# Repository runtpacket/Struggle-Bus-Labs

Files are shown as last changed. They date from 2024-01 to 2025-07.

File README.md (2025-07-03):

## Struggle Bus Labs V2.3824
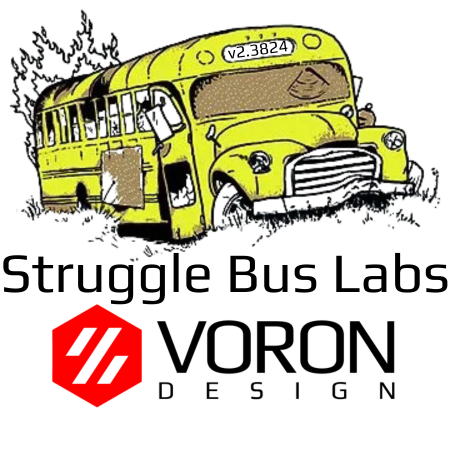
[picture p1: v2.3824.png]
Struggle Bus Labs


Come along and ride on a fantastic voyage with my Voron 2.4 350mm 3D Printer, I have named the Struggle Bus!

I hope you dont expect this to be cohert or organized.  this page is mainly for me to remeber thingds about my voron. 

## Build Log
Starting to prep for a toolhead change. Either XOl or Dragon Burner. Eitehr one will need filament cutter and runout sensor. Had an issues with end of sppol not coming of and jaming. this leaves the dub switch based fila runout in a good state. need to work on that. but next up  is https://github.com/bythorsthunder/Voron_Mods/tree/main/Wristwatch_Extruder_BMG

tonight I was playing with Multi Color printing. I tried all slicers each had littel quirks with thier setup for doing this. While researching I stumbled up 
[Single Extruder Tool Changer MMU with single exrtuder](https://github.com/strayr/klipper-fake-toolchanger/blob/main/README.md)

Setup is straight forward. Upload the klipper-fake-toolchanger.crg and add the include. then set up how many exturders in your slicer. no need to put M600 in for tool changer code as it will take care of that in th macro. Pretty slick. 

## My Build
Hoping to add the following to my machine this week
https://github.com/Thomas-3D/Front_Decontaminator
and an ERCF V2 with Happyhare in the future
https://github.com/moggieuk/Happy-Hare

[Formbot Voron 2.4R1 350mm Kit.](https://www.formbot3d.com/products/voron-24-pro-corexy-3d-printer-kit-with-hdmi-5-touch-screen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)

Dragon Std hot End, I print a lot of PLA. 5/11/2024 managed to kill both dragons. 1 grub screw fubared and on the other I snapped a nozzle off. Voron community helped me out and got me parts fast. now I am using a Bambu Labs Clone hotend. 

old mgn9's and mgn 12 will be as backer rod's to mitigate thermal expansion. 

Planning to use CPAP Fan for remote cooling with a 2.4 Top hat with rear umbilical

[Voron R2 Updates](https://github.com/VoronDesign/Voron-2/releases)

Frame Black. Primary printed parts color is black with KVP Galaxy Blue and Polymaker blue accents. I am using vinyl flat cap (blue and black) as rail fillers/cable covers.

X and Y upgraded to West 3d Berserker’s. [X rail](https://west3d.com/products/berserker-mgn12h-1r-300-350-400-linear-rails-viking-skis-with-carriages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) and [y Rails](https://west3d.com/products/berserker-mgn9h-1r-150-300-350-400-linear-rails-viking-skis-with-carriages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)

Z rails are Formbot vivedino's. The Berserker's were nice and clean when they arrived. I cleaned with ISO and lubed the rails with EP2. So far I have used 1/4 of the syringe. Lots left for maintenance. 

# Door Hinges
[Snap Latch removeable hinges ](https://www.printables.com/model/702768-kit-for-removable-panelsdoors-for-voron-v2trident-)

Finding the right hinges was a journey on the stuggle bus. A fun struggle as I had to try 5-6 hingle mods to get to a happy spot. I only like the snapping latches on the doors, for the panel I use magnetic panels clips and love them. My only issue is I sometimes forget about them and pull the panel off. So I have to hunt the floor for the clips. 

The Snap Latch removal hinges worked ok after a while. I am now using these The Pinned lift off hinges. https://www.printables.com/model/631351-vhb-lift-off-hinges-for-voron-trident-or-24

# Panel's

[Printed Solid ACM Panel Kit](https://www.printedsolid.com/products/voron-v2-panel-set-made-from-aluminum-composite-material)

Have not touched the stock PC Panels. Might use them in the future for another build.

# Printer Display 
[BTT LCD12864](https://www.printables.com/model/351939-voron-24-lcd-display-mod)

[BTT LCD12864 GitHub](https://github.com/bigtreetech/MINI-12864)

Stock Display panel didn't stay in down position and felt floppy.  very happy with this design. 

# Webcam

[Wansview 1080P web cam](https://github.com/runtpacket/Struggle-Bus-Labs/tree/main/Mods/WebCAM/wansview-1080p-camera-mount-model_files)

Pretty impressed with this $9 amazon special. Made me recall how crazy web cam prices got during covid. It would have been a $250 camera then. Lol

# Lighting

[2x270mm Disco on stick](https://github.com/VoronDesign/Voron-Hardware/tree/master/Daylight/Disco_on_a_stick_XXL)

[Disco Mount and Baffles](https://www.printables.com/model/315479-daylight-on-a-stick-mount)

Those worked well but I needed better diffusion. Printed these in Clear PLA. Will they hold up in a heated chamber? We shall See https://www.printables.com/model/617749-daylight-on-a-stick-diffuser
Need a couple of these to mount them https://www.printables.com/model/536772-daylight-on-a-stick-mount other places the stock daylight clip worked better. 

[Rainbow Barf](https://wiki.kb-3d.com/en/home/linneo/voron/harnesses/RainbowBarfLEDHarness)

# Filament Runout Sensor

[BTT Smart Filament Sensor](https://github.com/bigtreetech/smart-filament-detection-module/tree/master/V1.0)

Needs lubed and shimmed. Turned off as I need to troubleshoot false positives..
got into troubleshooting. wow was figuring it out a pita. of course once I got it working. I find the perfect how to guide and mounts. https://github.com/VoronDesign/VoronUsers/tree/main/printer_mods/Empusas/BTT_Filament_Motion_Sensor_Mount

# Klipper add-ons

[Jontek2 better Print Start](https://github.com/jontek2/A-better-print_start-macro)

[Kamps](https://github.com/kyleisah/Klipper-Adaptive-Meshing-Purging)

[LED effects](https://github.com/julianschill/klipper-led_effect)

# Fans

[Nevermore v5 Duo](https://github.com/nevermore3d/Nevermore_Micro/tree/master/V5_Duo)

[Resmed CPAP Fan mod by OverLord6920](https://github.com/runtpacket/Struggle-Bus-Labs/tree/main/Mods/CPAP%20FAN)

[Ellis bed Fans](https://github.com/VoronDesign/VoronUsers/tree/master/printer_mods/Ellis/Bed_Fans)

# Probe

[Chaotic Labs Tap v1](https://github.com/Chaoticlab/CNC-Tap-for-Voron)

1/29/2024 - During gantry rail upgrade I hulked a screw on the belt holder. sometimes I don’t know my own strength. Special not CL v2 is incompatible with the Mellow Fly Canbus board. Need to go through parts I may have a printed tap and all the bits and pieces needed to get back to printing. 

2/19/204 - Ended up with a work around in place. I put a dab of super glue on the screw threads. it's working fine and I got a decent belt tune according to kippain-Shake and tune. Printed like a dream for a week and then it looked like wavy lines and under extrustion. found toolhead had a wobble. tore down to tap and foudn 1 screw loose. put blue thread locker on and tighened. 1 week later same issue. I hate tearing down to Tap. everytime I do i end up crimpin cables or havingt o buy something I borked. tonight I had to swap the hotend out. I think the dragon end I had on (reminder for self CHT nozzle) has a bad thermistor as I was getting Heater extruder not heating at expected rate. pid tune calibration didn't help (reminder to self fans on). items borked: X endstop wire broke at switch leg. So I went sensorless homing as it was on my todo list. I only installed endstop with canbus becuase I was already running cables. (remind one day remove the endstops and wiring and relocation pieces). hardest part was following directions. could not understand the one section on driver tuning. got help on discord. worked though those issues. tried to make a spare TAP wire. As i have broken them twice now. no success need to check wiring when my eyes are better. So far I like sensorless homing. even if the homing speed is SLOW. it's less wires for me to break. Oy yeah remider to self. SB FAN board is not screwed in. If you screw it in it doesn't work. get some button head 10mm I think the socket heads are too tall and stop it from fully seating. 

IMPORTANT! If you use a SB 2 Piece toolboard. You this https://www.printables.com/model/642001-voron-stealthburner-sb2209-misalignment-protector

# CanBUS

[Esotericals canbus guide](https://github.com/Esoterical/voron_canbus)

[BIGTREETECH U2C V2.1](https://github.com/bigtreetech/U2C)

[Mellow Fly SB2040 v1 KB3D Guide](https://wiki.kb-3d.com/home/mellow/voron/mellow_sb2040)

[Mellow SB2040v1](https://github.com/Mellow-3D/Fly-SB2040)

Mellow Fly SB2040 V2 released the magic smoke. I had just started a print and watched the printer start to home when I saw the smoke. Opened up the stealth burner to find a capacitor was missing. It looked to be cold soldered. This led to a mosfit spewing it's guts. Fast replacement thanks to KB3D.

The Mellow Fly SB2040 v1 and v2 are incompatible with the Chaotics Labs CNC Tap V2. 

IF you use any SB toolhead board thats 2 piece you NEED this! (you can kill the boards if you misalign, this saves you from yourself) https://www.printables.com/model/642001-voron-stealthburner-sb2209-misalignment-protector

# Umbilical

I built my umbilical cable using 2mm PTFE alongside the SB2040 Canbus cable inside 1/8" Sleeving. So far I find the PTFE to be perfect. 

[No Longer use - A Drive pg7 Mount](https://www.printables.com/model/312008-voron-24-a-drive-pg7-umbilical-mount)

[Minsekt Y Endstop relocation](https://github.com/VoronDesign/VoronUsers/tree/master/printer_mods/Minsekt/Rear_Umbilical/Y_Endstop_Relocation)

[Z Chain relocation](https://www.printables.com/model/279739-voron-can-bus-z-chain-move)

# Flex Plate Holder

[Voron V2.4 Flex Plate Holder by KeiranSolaris](https://www.printables.com/model/163992-voron-v24-flex-plate-holder)

# Panel Clips

[Magnetic Panel Clip for Voron 2.4 by FunFunboy](https://www.printables.com/model/84734-magnetic-panel-clip-for-voron-24)

# Skirt 

[Hexagon skirt inserts by Tom van der Geest](https://www.printables.com/model/648945-voron-24-skirt-insert)

# Misc

Z belt Covers are done. https://www.printables.com/model/479809-voron-24-z-belt-covers

Purge Bucket and Nozzle brush With plate Stop https://www.printables.com/model/479809-voron-24-z-belt-covers 
goes very well with https://www.printables.com/model/346782-voron-24-bed-alignment-stop-updated
 
## Coming Soon

[2.4 Tophat](https://www.printables.com/model/571759-voron-24-trident-magnetic-tophat-35mm-66mm-beta-re)

[CPAP for Voron 2.4 and Stealthburner](https://github.com/ogland/Printer-mods/tree/main/V2/CPAP)

[Rear Umbilical Passthrough](https://github.com/tanaes/whopping_Voron_mods/tree/f64cd56fe2baac4348ac56e3d0e70f4577013d7e/umbilical_passthrough)

[Skirt Buttons](https://www.fysetc.com/products/fysetc-hot-key-board-voron-skirt-button-pcb-voron-skirt-klipper-pre-installed-pcb-board-with-neopixel-led-for-voron-v2-4-trident-swit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)

[Replacing SB2040 V1 with SB2040 V2](https://github.com/Mellow-3D/Fly-SB2040/tree/main/V2/Hardware)

[Exhaust to Basement Window](TBD)

[Reusing old mng9 / mgn12 rails as backers](https://github.com/VoronDesign/VoronUsers/tree/master/printer_mods/whoppingpochard/extrusion_backers)

## Changes I am considering 

[The Filter](https://github.com/nateb16/VoronUsers/tree/master/printer_mods/nateb16/THE_FILTER)

[Monolith Panels](https://github.com/CloakedWayne/Monolith_Panels/blob/main/Images/distant_view.png)

[Clicky Clacky Door](https://github.com/tanaes/whopping_Voron_mods/tree/main/clickyclacky_door)

[The Filter]([https://github.com/tanaes/whopping_Voron_mods/tree/main/clickyclacky_door](https://www.printables.com/model/334276-the-filter-for-voron-24))
[jst hub for the filter](https://www.printables.com/model/512527-jst-hub-for-the-filter)

[Wago and jst bed mount 2020](https://www.printables.com/model/512516-wago-and-jst-bed-mount-for-2020)

## Tools I like
[GT2 Belt Tensioner](https://github.com/Diyshift/3D-Printer/blob/main/GT2%20Belt%20Tension%20Meter/Manual/GT2_Tensiometer_Manual.pdf)

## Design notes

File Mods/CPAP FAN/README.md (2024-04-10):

# Remote Cooling using a Resmed CPAP Fan 

This will need some tape to seal air leaks. i used 1mm foam and the base needs glued to the pump bottom.

## Requires: 
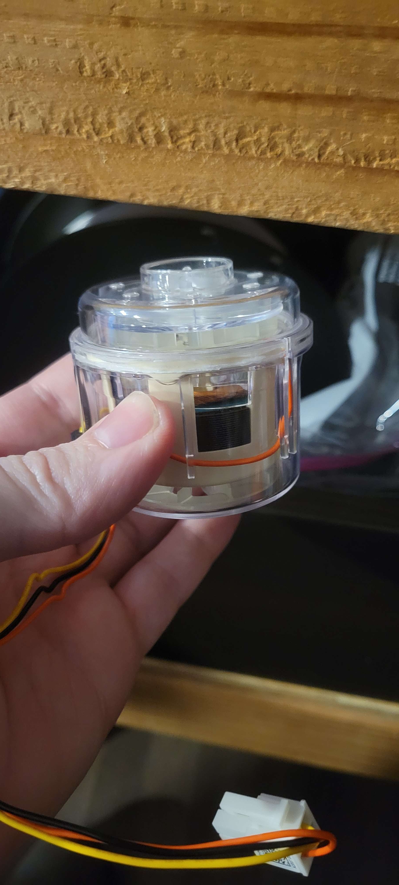
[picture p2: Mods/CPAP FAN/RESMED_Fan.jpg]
RESMED CPAP Fan


[Fan speed controller on amazon](https://www.amazon.com/dp/B087M3GVYX?ref=ppx_yo2ov_dt_b_product_details&th=1)

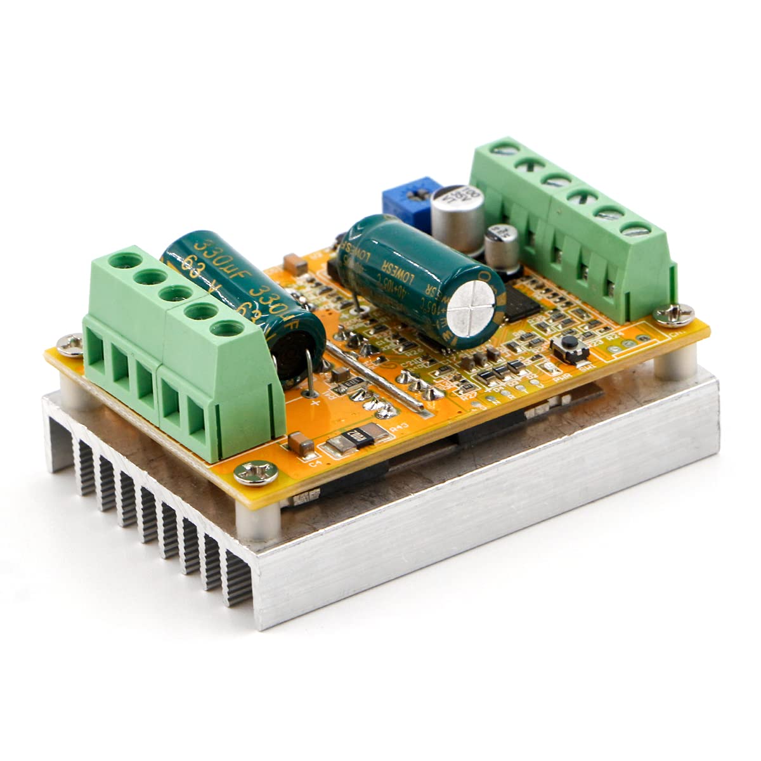
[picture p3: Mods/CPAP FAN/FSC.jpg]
RioRand 300W 5-50V PWM DC Brushless Electric Motor Speed Controller with Hall-Less


# Optional

[BME280 Temp Pressure Humidity Sensor](https://www.amazon.com/dp/B01N47LZ4P?psc=1&ref=ppx_yo2ov_dt_b_product_details)

I am considering chaning this out to the BME680 so that I can monitor in chamber VOC.

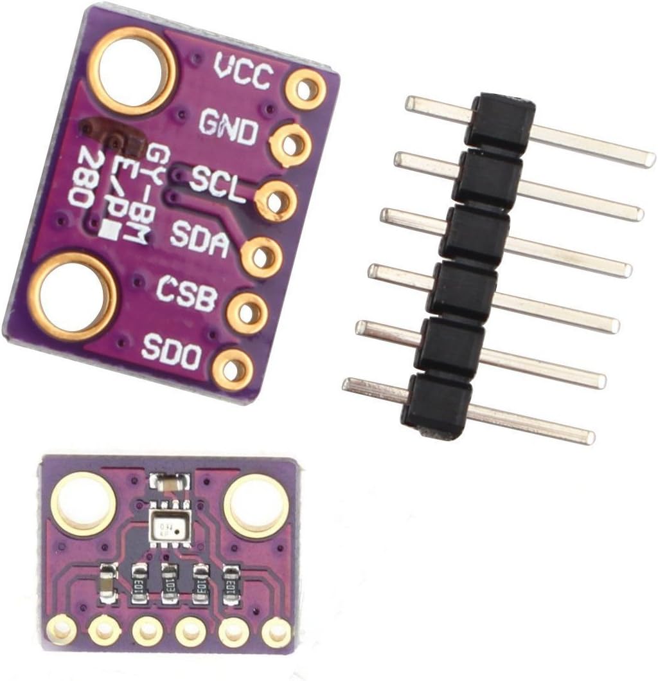
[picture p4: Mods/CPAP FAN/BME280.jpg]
BME280 Temp Pressure Humidity Sensor


## Klipper configuration. Add this to your printer.cfg
```
[fan]
pin: PB6
hardware_pwm: True
shutdown_speed: 0
kick_start_time: .25
max_power: 1 # adjust below 1 if you would like the max speed to be slower
off_below: 0.06 # minimum speed where the fan starts spinning - on octopus pro this is correct - will be lower maybe 0 on mellow Super 8 because of different GPIO pullup and protection resistors
cycle_time: .0001 # = 1khz - CPAP fan driver recommended range is 2-50khz
#tachometer_pin:^PG13
#tachometer_ppr: 2
```

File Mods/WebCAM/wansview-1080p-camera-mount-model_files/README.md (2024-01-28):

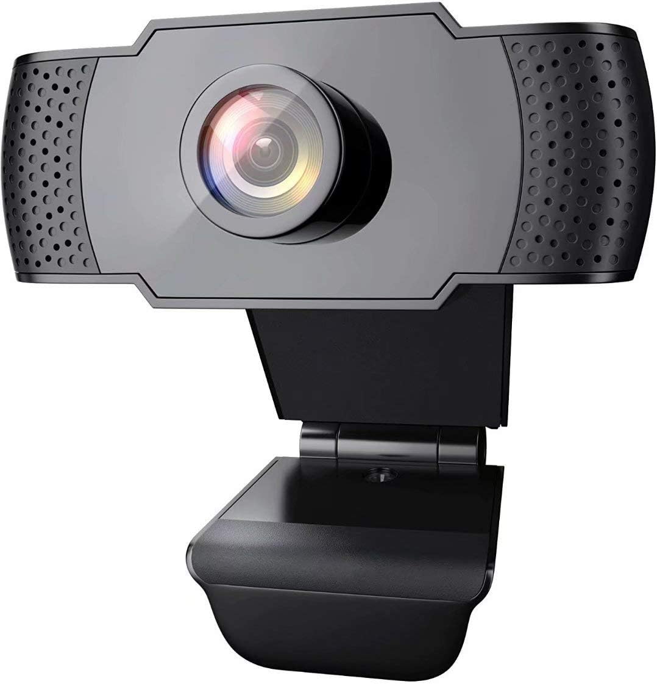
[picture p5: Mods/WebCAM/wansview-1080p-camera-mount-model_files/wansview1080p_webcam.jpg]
Wansview 1080p webcam


[Wansview 1080p webcam](169990-wansview-1080p-camera-mount.pdf)

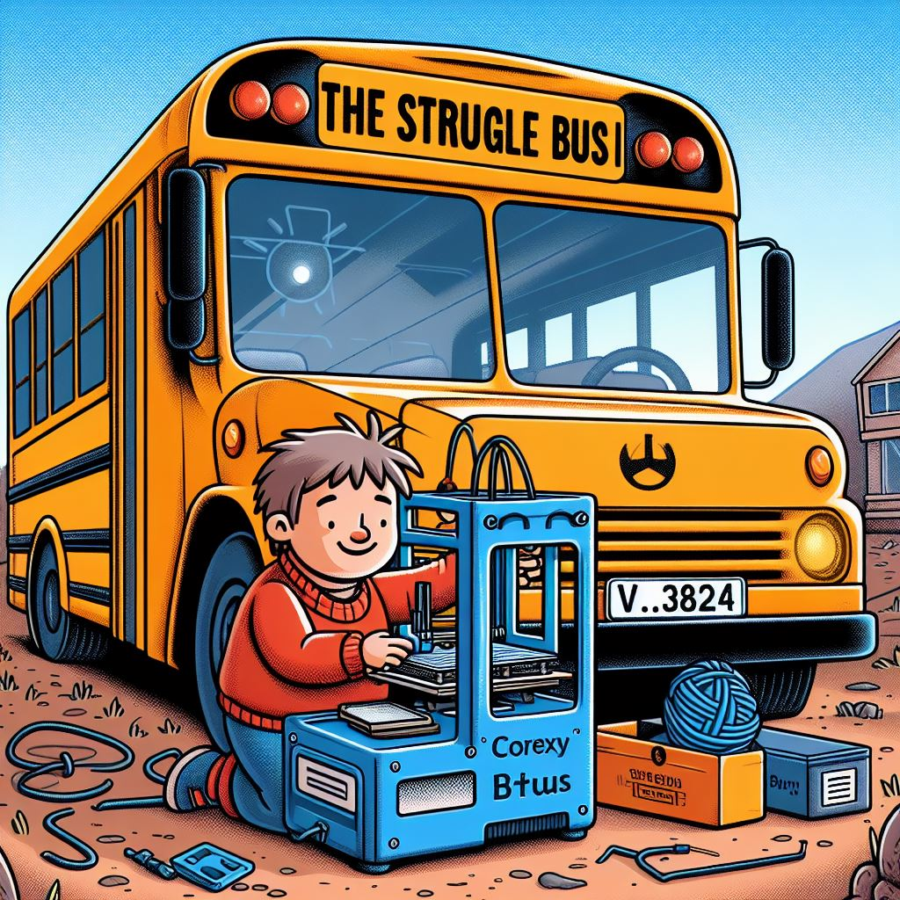
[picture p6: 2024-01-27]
SBL.jpg

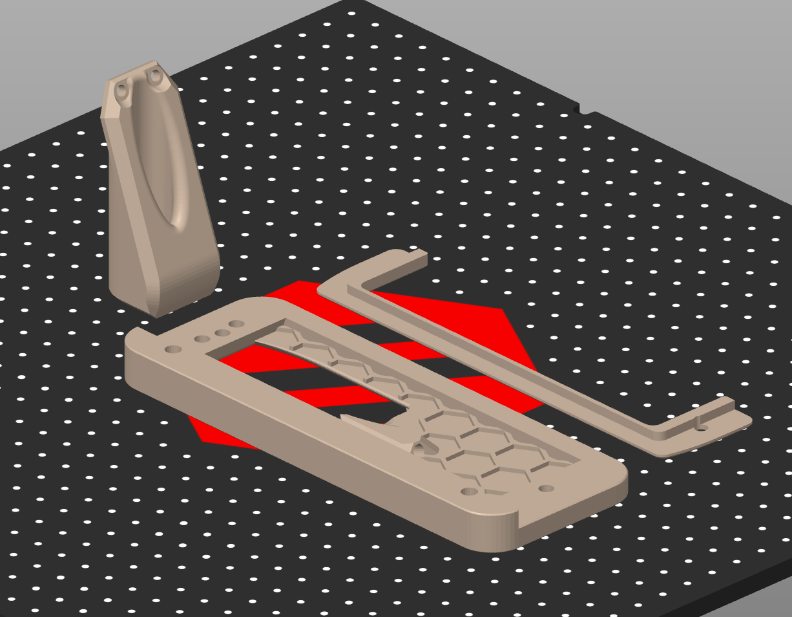
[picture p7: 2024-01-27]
Mods/umbilical_passthrough/Images/part_orientation.png

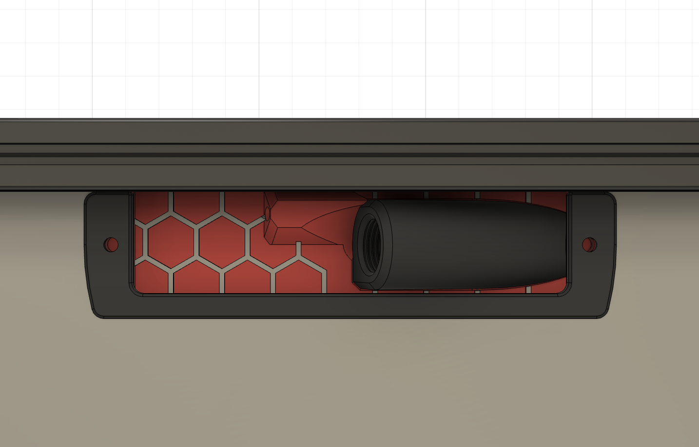
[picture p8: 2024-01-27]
Mods/umbilical_passthrough/Images/front.png

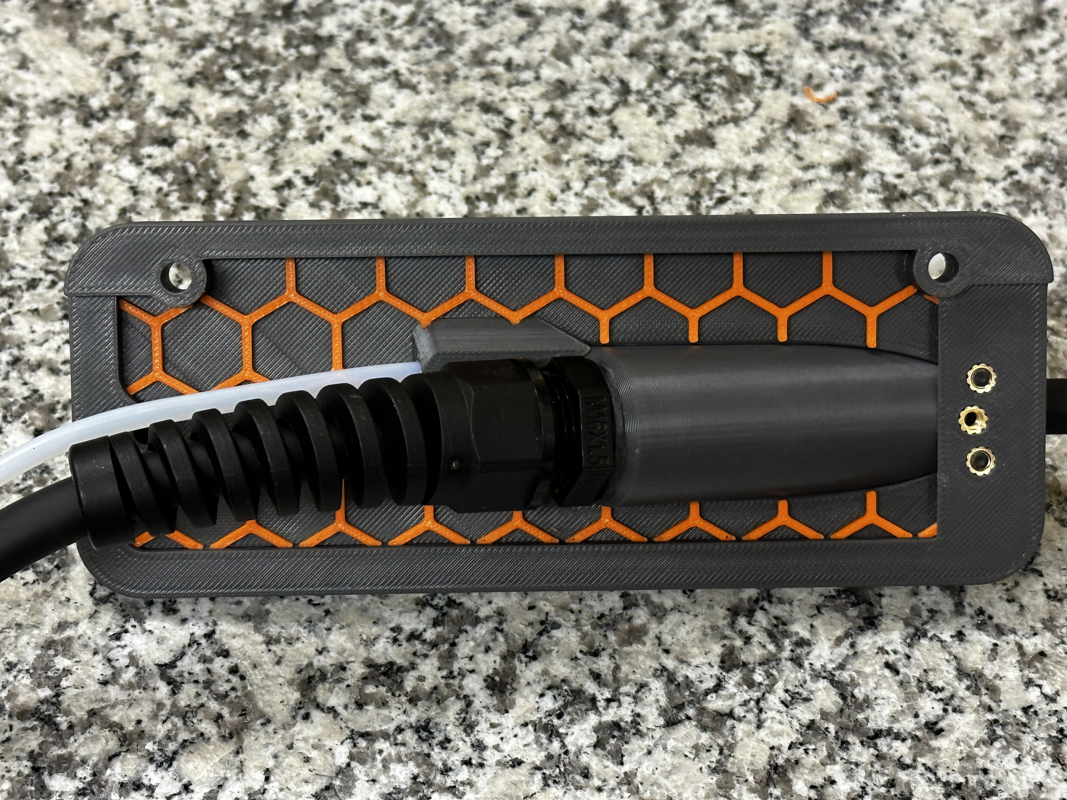
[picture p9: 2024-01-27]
Mods/umbilical_passthrough/Images/with_gland.jpeg

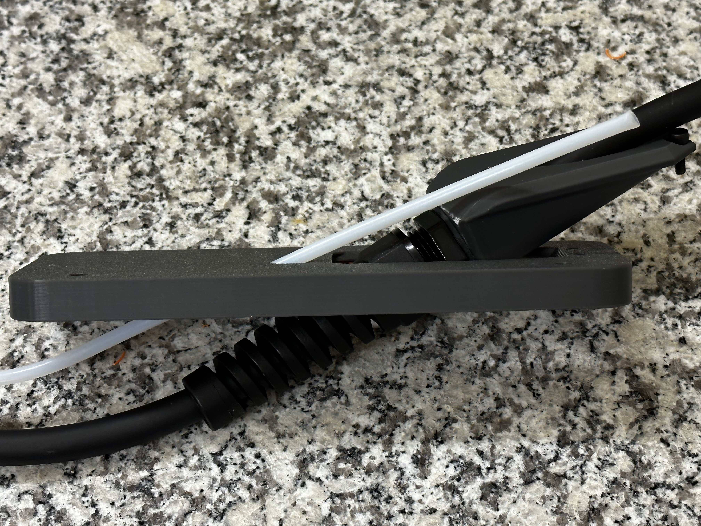
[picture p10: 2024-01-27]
Mods/umbilical_passthrough/Images/top_disconnected.jpeg

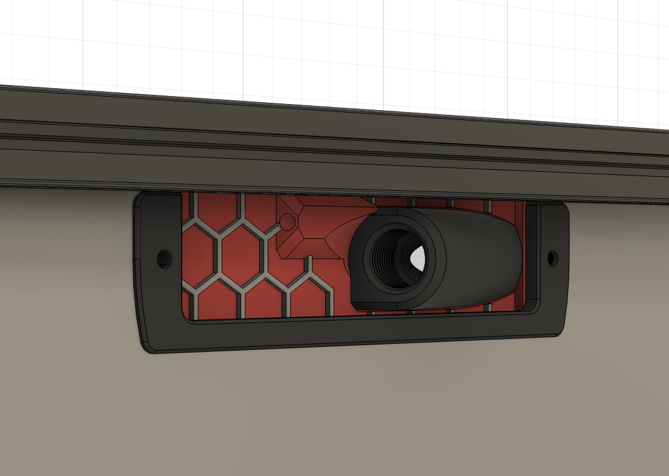
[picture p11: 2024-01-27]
Mods/umbilical_passthrough/Images/front_quarter.png

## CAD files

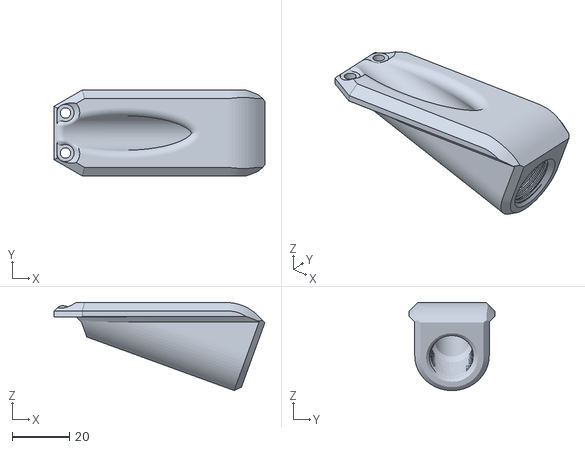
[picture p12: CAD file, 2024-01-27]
Mods/umbilical_passthrough/STLs/M16_cable_gland_housing.stl
73.6 x 30.0 x 30.7

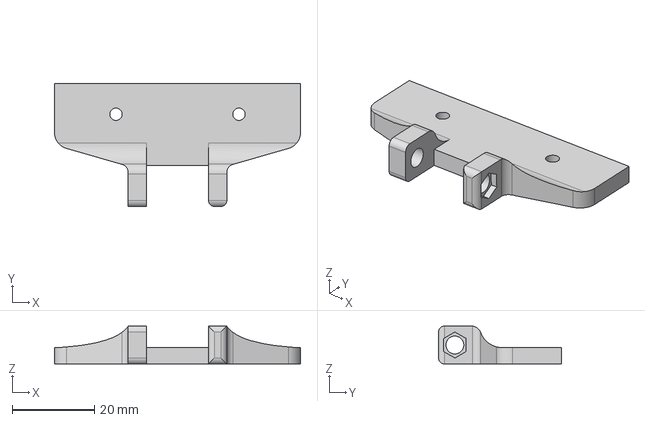
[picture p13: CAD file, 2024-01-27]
Mods/WebCAM/wansview-1080p-camera-mount-model_files/voroncammount.step
60.0 x 30.0 x 9.26 mm

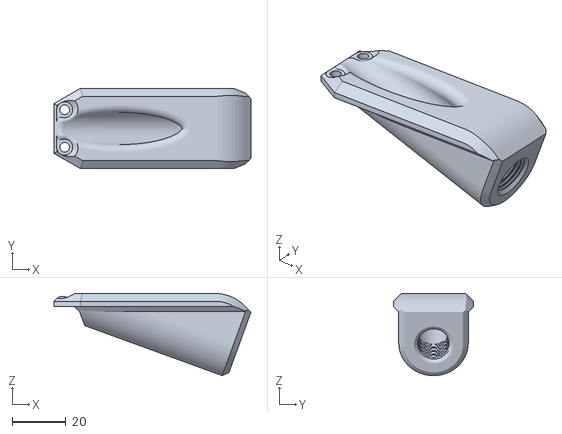
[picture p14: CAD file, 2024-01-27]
Mods/umbilical_passthrough/STLs/PG7_cable_gland_housing.stl
73.6 x 30.0 x 30.7

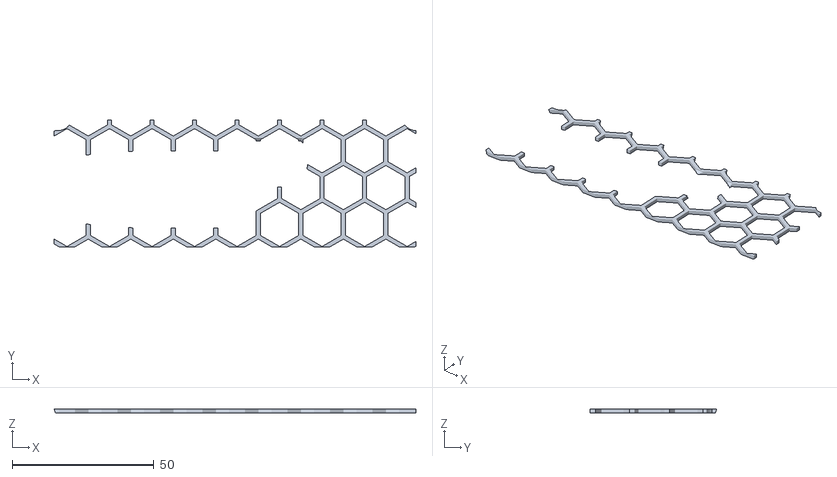
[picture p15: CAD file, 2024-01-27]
Mods/umbilical_passthrough/STLs/Hex Accent.stl
127.7 x 44.6 x 1.40

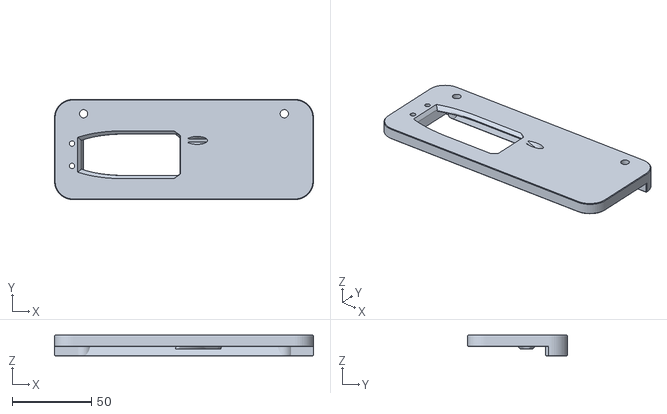
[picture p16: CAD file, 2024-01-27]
Mods/umbilical_passthrough/STLs/UmbilicalBlankingBackPlate-L-6mm.stl
163.0 x 63.0 x 13.0

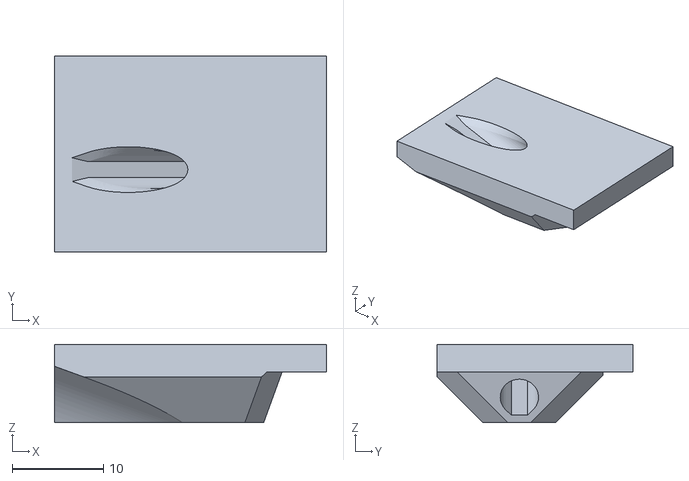
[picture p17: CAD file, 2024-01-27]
Mods/umbilical_passthrough/STLs/PTFE_fit_test.stl
29.8 x 21.4 x 8.55

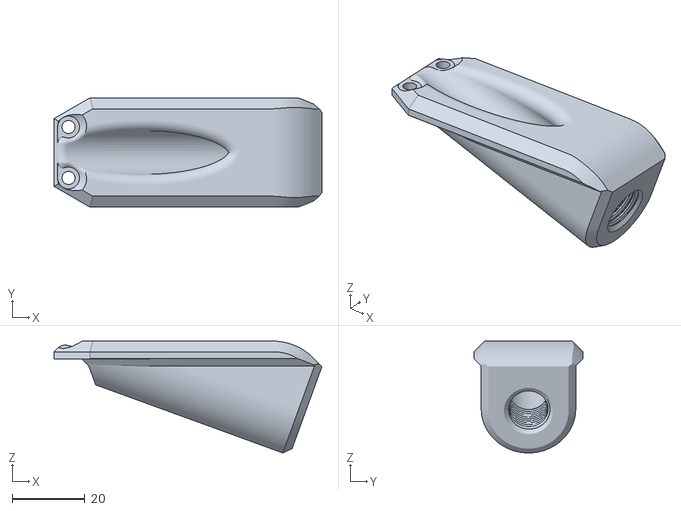
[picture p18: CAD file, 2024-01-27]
Mods/umbilical_passthrough/STLs/M12.5_cable_gland_housing.stl
73.6 x 30.0 x 30.7

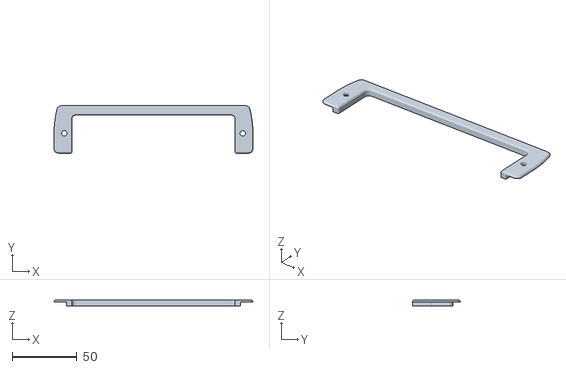
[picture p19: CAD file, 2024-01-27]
Mods/umbilical_passthrough/STLs/Front_Plate.stl
154.0 x 36.8 x 4.60

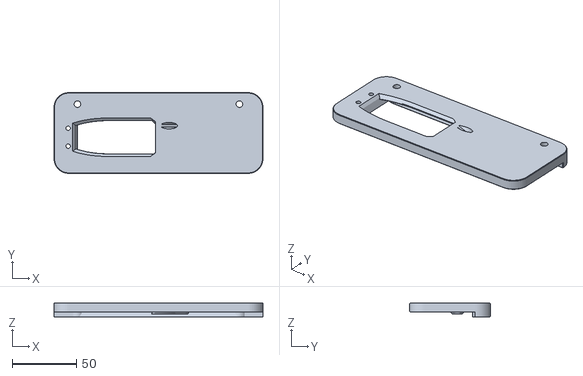
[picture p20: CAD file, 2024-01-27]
Mods/umbilical_passthrough/STLs/UmbilicalBlankingBackPlate-L-4mm.stl
163.0 x 63.0 x 11.0

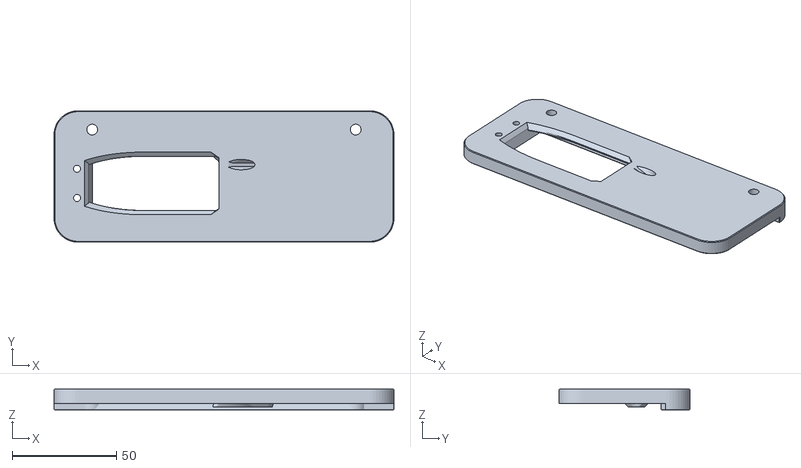
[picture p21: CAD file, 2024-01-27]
Mods/umbilical_passthrough/STLs/UmbilicalBlankingBackPlate-L-3mm.stl
163.0 x 63.0 x 10.0

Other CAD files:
Mods/CPAP FAN/V2-CPAP-BME285_cover_v5.f3z
Mods/CPAP FAN/V2-CPAP-normal_cover_v3.f3z
Mods/WebCAM/wansview-1080p-camera-mount-model_files/voroncammount.f3d
Mods/WebCAM/wansview-1080p-camera-mount-model_files/voroncammount.stl
Mods/umbilical_passthrough/CAD/umbilical_passthrough_backing_plate.f3d

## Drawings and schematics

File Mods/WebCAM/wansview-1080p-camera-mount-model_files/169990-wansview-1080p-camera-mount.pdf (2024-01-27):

## Wansview 1080p

## Camera mount

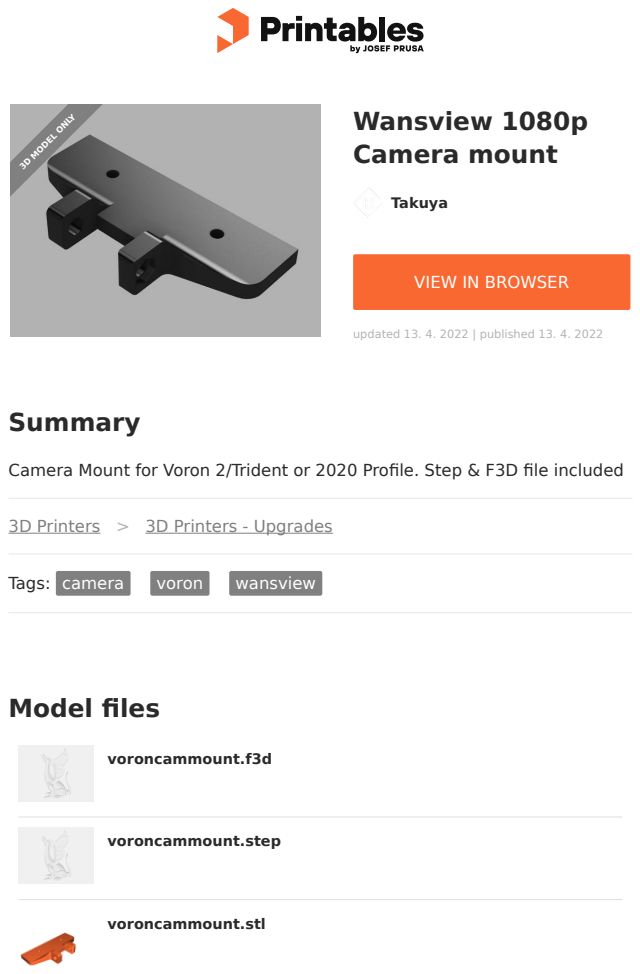
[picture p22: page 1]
Model files; Summary; 3D Printers; 3D Printers - Upgrades; Tags: camera; voron; wansview; Takuya; updated 13. 4. 2022 | published 13. 4. 2022; voroncammount.f3d; voroncammount.step; voroncammount.stl; 3D MODEL ONLY

VIEW IN BROWSER (https://www.printables.com/model/169990-wansview-1080p-camera-mount)

Camera Mount for Voron 2/Trident or 2020 Profile. Step & F3D file included

## License

This work is licensed under a

Creative Commons (International License)

Public Domain (https://creativecommons.org/share-your-work/public-domain/cc0/)

### ✔ | Sharing without ATTRIBUTION

✔ | Remix Culture allowed
✔ | Commercial Use
✔ | Free Cultural Works
✔ | Meets Open Definition

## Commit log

2024-01-27 upload
    1st update
    [Front_Plate.stl, Hex Accent.stl, M12.5_cable_gland_housing.stl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]
2024-01-27 file Upload
    [voroncammount.f3d, voroncammount.step, voroncammount.stl]
2024-01-27 upload image of fan
2024-01-27 upload image of motor speed controller
2024-01-27 Upload readme for CPAP Fan
2024-01-27 Upload klipper section
    [Add_to_printer_config.txt.txt]
2024-01-30 add plate pictures
